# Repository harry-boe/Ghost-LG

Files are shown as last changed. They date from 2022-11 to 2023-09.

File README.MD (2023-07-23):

# Ghost LG Toolhead - RC2 18.07.23

## A V0 Toolhead using LGX Gears

| Ghost LG - Gearbox without front section to show Bondtech LG gears arangement | 
|--- |
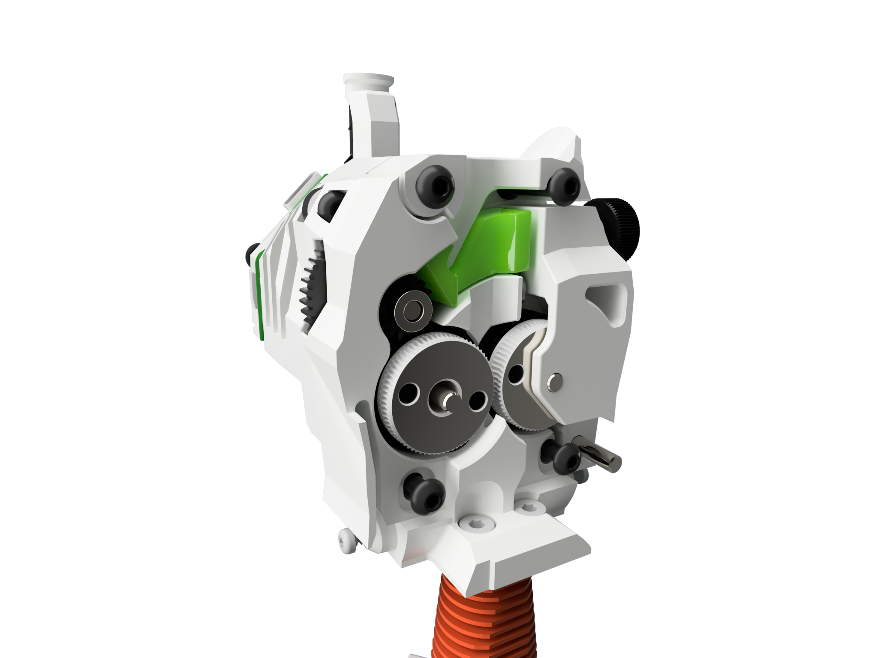
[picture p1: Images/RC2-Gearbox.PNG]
|  | 

This is the release candidate 2. This release is the result of extensive testing and pushing the toolhead to the limits.
Well i found the limits and started melting the plastic parts due to excessive stepper temps. And that's where this release kicks in.

Changes:
- Gearbox
  - Updated and strengthened idler
  - Updated beefier latch shuttle
  - Updated mid-section adopted to the new latch shuttle
- Motor Cover
  - Updated EBB35 mount with improved cooling and ventilation cut-outs
  - Updated pancake PCB mount 
- Cowling
	- Multiple minor changes to eliminate thin walls
	- Fix: Pinda probe mount. I did not had a Pinda probe to test so the old version mount was 1mm to small (diameter)

## Variations

### Hotends 

- Dragon style mounts 
    There are several hotends available that use the Drogon type mounting pattern including the Dragon itself, the dragon fly, Lizard, Lizard pro and others. In fact most of my testing was done with a red lizard
- Revo
  Currently one of the mor popular changes. The cowling as 2mm longer to adapt for the longer hotend. This version should provide improoved cooling as the smaller heat block allows for more airflow.

### Bed probes

- Euklid probe
  Most of my testing was done wit this probe. It looks kind of wierd but it works verry well.
  I'm using this probe with my Servo-Klicky dock.
- Zero Klick
  Another popular choice in the Ant printer universe.
  Should work as well with Servo Klicky dock and the standard Zero Klick docking solutions.
- Pinda Probe (SuperPinda)
  Inductive Probe if you don't like to deal with probe docking solutions

# Some impressions

| Ghost LG Toolhead | |
|--- |--- |
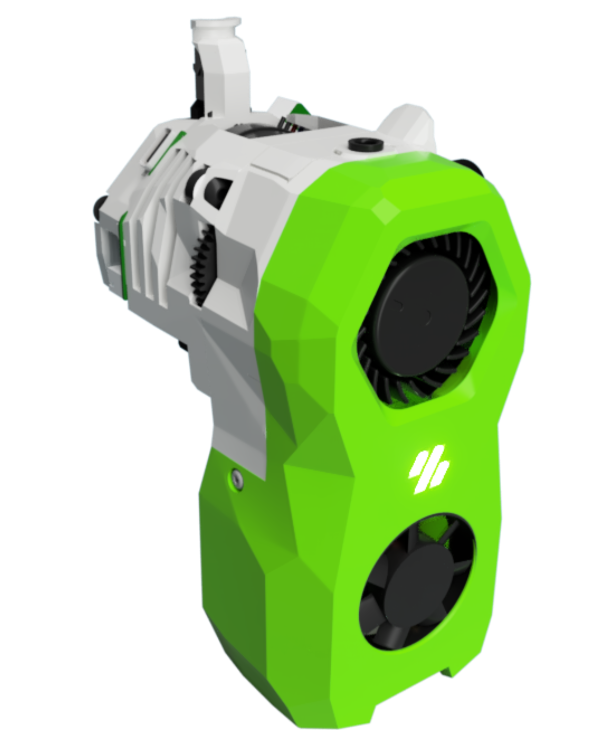
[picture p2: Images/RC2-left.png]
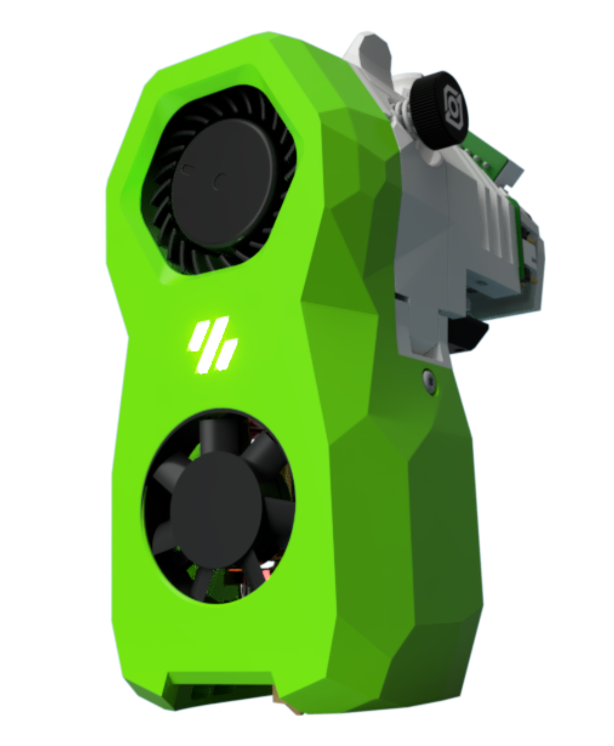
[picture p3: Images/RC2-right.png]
|  |  |

| Multiple Hotend and Probes | |
|--- |--- |
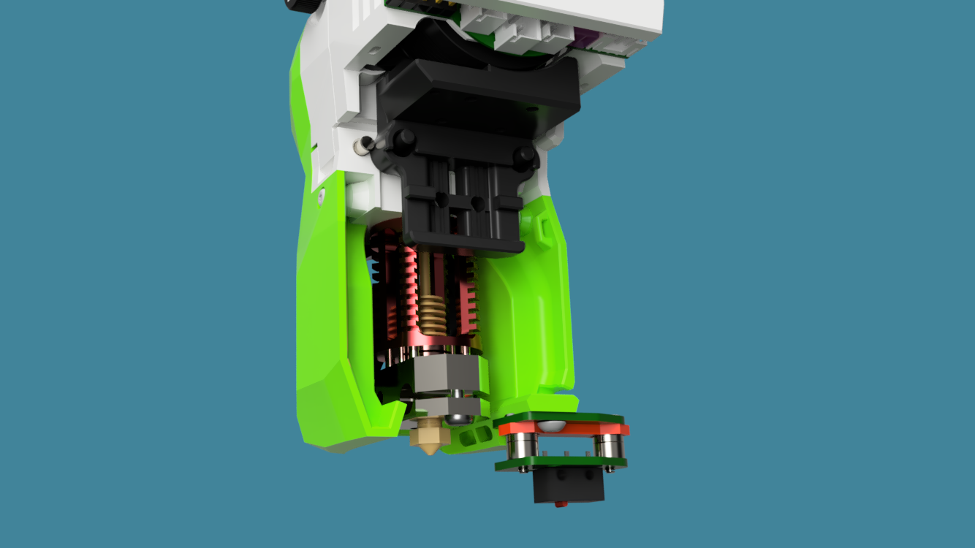
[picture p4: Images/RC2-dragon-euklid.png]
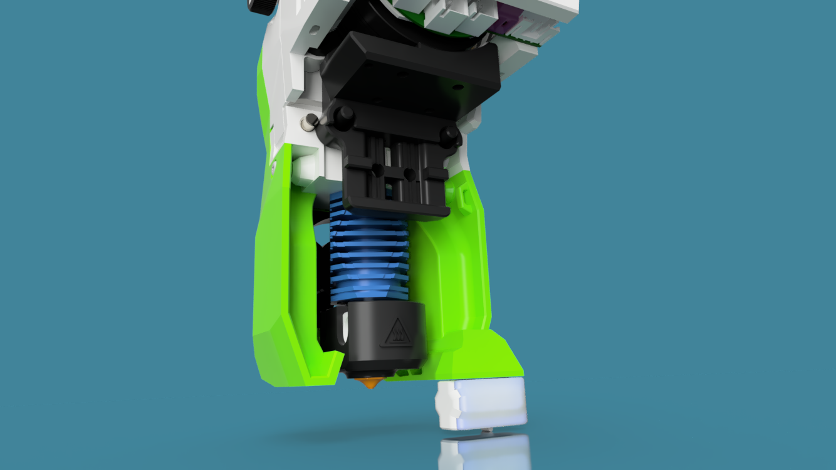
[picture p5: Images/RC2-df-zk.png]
|  |  |
| Dragon Hotend / Euklid Probe | Dragon-Fly / ZeroKlick Probe |
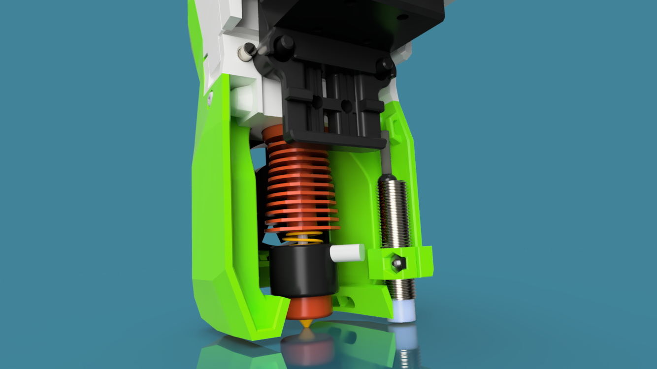
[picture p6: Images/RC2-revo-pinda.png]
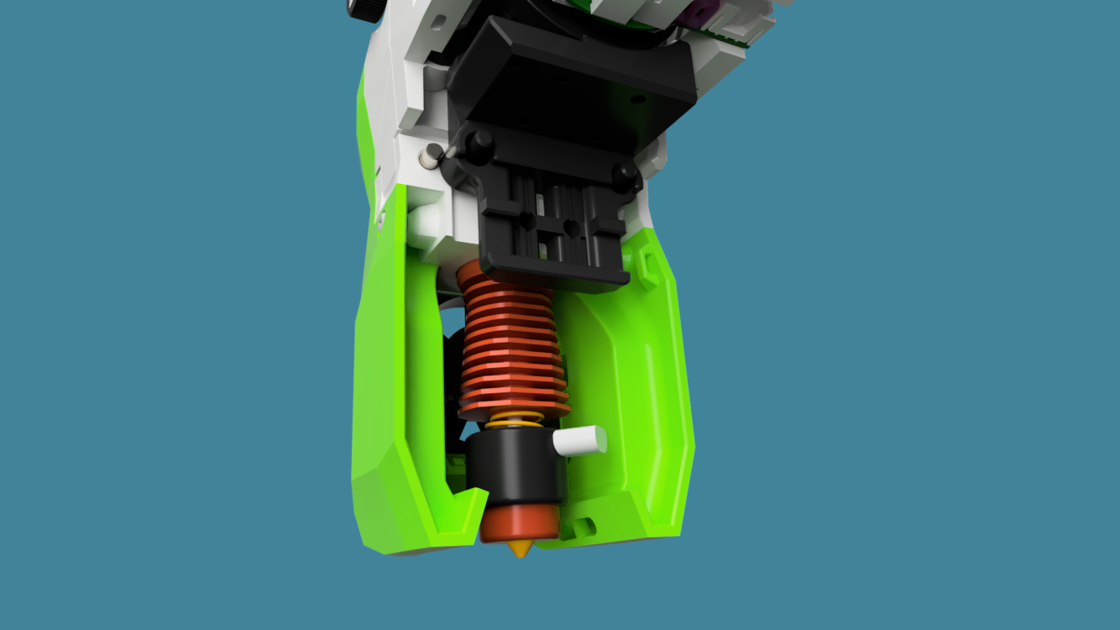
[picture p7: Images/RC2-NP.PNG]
|  |  |
| Revo / Pinda Probe | Revo / No Probe |

## Design Goals

-	Print Quality: 

    The Mini AB is hard to get right. Misalignment on the drive gears and also potential of centric gears due to the set screws affect print quality The LGX Gears solve this problem by running on needle bearings and not using set screws. They can also move axial on the bearings, which basically means that they are self-adjusting.
-	Maintain MINI AB footprint 

    At least on the important dimensions which are
	- Mount to front
    - Distance to Top (to maintain clearance with top-head)
    - Width (especially for IDEX use) 

The Ghost LG maintains those measurements by being 3mm smaller on width Distance to the back is +5mm (there is enough room here) Distance to the nozzle end is +4mm dragon and +6mm Revo. This means that the bed needs to be lowered by those distances. This is no Issue for the V0 and most of the Ant printers.

- Voron Design language Well basically the new stealth design

- Optimized for IDEX Minimize with (-3mm) Nozzle height adjustment. There is a slot for the mounting screws to the X-carriage to enable some height adjustment.

- Easy to assemble

## Printing notes

All parts print with standard Voron settings and no supports.
However the parts have fine details and tight tolerances. Make sure you printer is erll calibratd and use reasonable print speeds
Consider a brim for the EBB mount as the contact patch on the print bed is very small

## BOM

The project is stoill in its early stage so the BOM is subject to changes.
However I try to maintain the items below for the final design.

### Required Parts

| Item 	| Amount 	| Sourcing 	| Notes 	|
|---	|---	|---	|---	|
| HGX-Lite Etruder Gear Kit 	| 1 	| https://www.aliexpress.com/item/1005004699143725.html 	| Provided 3mm pins can be used but do not allign with case 	|
| 4015 Turbo Blower 40x40x15MM 	| 1 	| https://www.aliexpress.com/item/1005004909471864.html 	| Modifcation required  |
| 3007 axial fan 	| 1 	| 	|  |
| Hotend 	 | 1 	| Phaetos Dragon  	|  Revo in preparation |
| Nema 14 36mm pankake stepper motor	 | 1 	| 17mm or 20mm  	|  use the right rear cover  |
| M3x18 BHSC 	| 2 	| 	| 	|
| M3x20 BHSC 	| 2 	| 	| 	|
| M3x6 BHSC 	| 4 	| 	| 	|
| M3x6 countersunk flat head screws 	| 3 	| 	| 	|
| 2x8 or 2x10 self tapping screw 	| 2 	| 	| 	|
| M3 Heat Inserts | 6 	| 	| 	|
| PTFE Tube 	| 17mm | 	|  	 |

### Optional Parts

| Item 	| Amount 	| Sourcing 	| Notes 	|
|---	|---	|---	|---	|
| Individual NeoPixels 	 | 2 	| https://learn.adafruit.com/adafruit-neopixel-uberguide/individual-neopixels	| 	|
| 3x15mm Pin | 3 | https://www.aliexpress.com/item/1005002473550667.html | For those who want the pins alligned with the case |
| Omron Mouse Button - Micro Switch | 1 | | For filamentsensor (if üpossible) |
| 4.5 mmm Stainless Steel Solid Ball | 1 | https://www.aliexpress.com/item/1005004091669583.html | For filamentsensor (if üpossible) |

# Older Versions

# Ghost LG Toolhead - RC1 - 5.1.23

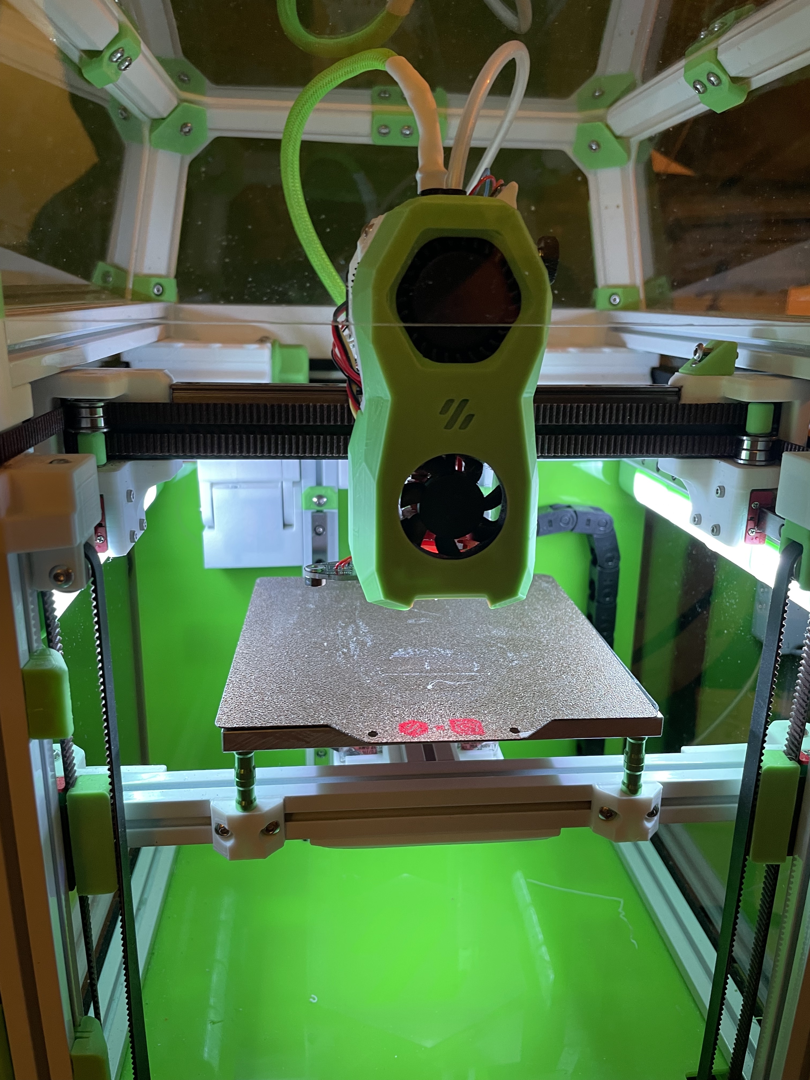
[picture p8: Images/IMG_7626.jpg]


New Features:

- Various cowling covers with mounts for probes
    - Euklic Probe - This is the one the I was using during the beta tests
      I'm using the euklid probe with my ServoKlicky dock
    - ZeroClick - mount for zruncho's clicky probe. The position as derived from the MiniAB, so it should work with the docks
    - PINDA inductive probe. Popular probe used on the Prusa MK3 printers. Maybe not the most accurate but defiantly the most hassle free installation.
      No Dock or complex macro definitions required. Not the klipper currently does not support the 4 wire probe with temp compensation in the firmware.
      If you like to have temp compensation make shure you order a Super PINDA (https://www.aliexpress.com/item/1005004488098625.html)
    - and last but not least a cover without any probe mounts

- New diffusor for Logo LED 
    - Maybe not for everybody as wiring is not easy.

- Anti squish adjustment thingy 
    - I don't think that's a requirement but a added one because this as popular right now

- Mounting screws for the cowling
    - The click on cowling came off a few times during my tests. So I added some self-tapping screws to mount it on the gearbox.
      This makes the whole toolhead way more rigid which is especially important for all cowling that have probes attached

Enhancements

- Cowling
    - fighting thin walls. Lots of tweaks here and there to improve printability 
    - New fan ducts. They are now moved forward like on the MiniSB. This allows for probe mounts without impact on the air channels
    - Improved air channels.
        The overall cooling performance is surprisingly good. But there was less cooling on the front side of the prints.
        The new air channels provide better flow in that area
    - Wiring channels
        The toolhead is now 2mm wider at the rear center (still same footprint). This creates more room for the wires exiting the toolhead
        Wire channel for cooling fan and nozzle LED redesigned.
        This section has now a break-away support which allows to route the wires without heaving to rempove the connectors.
        Also the cable channels are increased in size
    - Some minor design tweak on top of the toolhead for aesthetic reasons

- Gearbox
    - As mentioned the gearbox is now 2mm wider mid center (it not really visually noticeable)
    - Much wider cable channels to simplify wiring
    - New Latch geometry.
        The latch now pushed the idler back when opened (was a community suggestion)
    - Strengthened latch shuttle
    - Mid and rear section are bolted together with a countersunk screw.
        This make the toolhead much more rigid
    - Small changes on the idler to provide access to the anti-squish thing
    - the standard bowden collet is now the one from bondtech. It's much smaller and works better

- Board Mounts
    - EBB36 Mount
        - added a zip mount for the heater and thermistor wires
        - added a zip mount for the CANbus cable to eliminate stress on the connector and wires
    - The other mounts have no changes

## RC1 with EBB36 mount
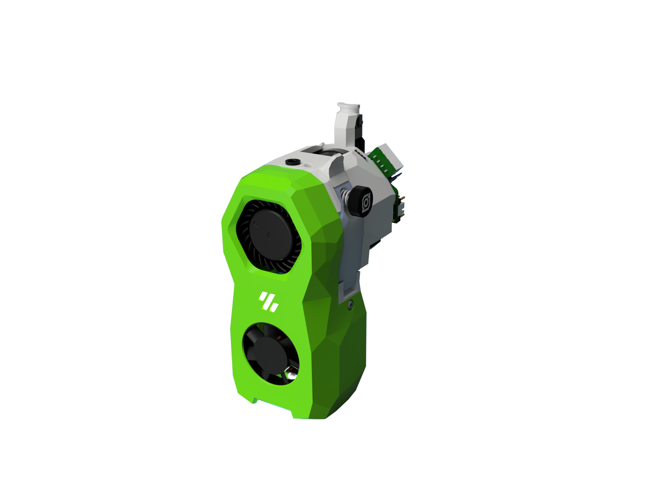
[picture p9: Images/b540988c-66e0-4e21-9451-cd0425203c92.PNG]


## PINDA Probe mount
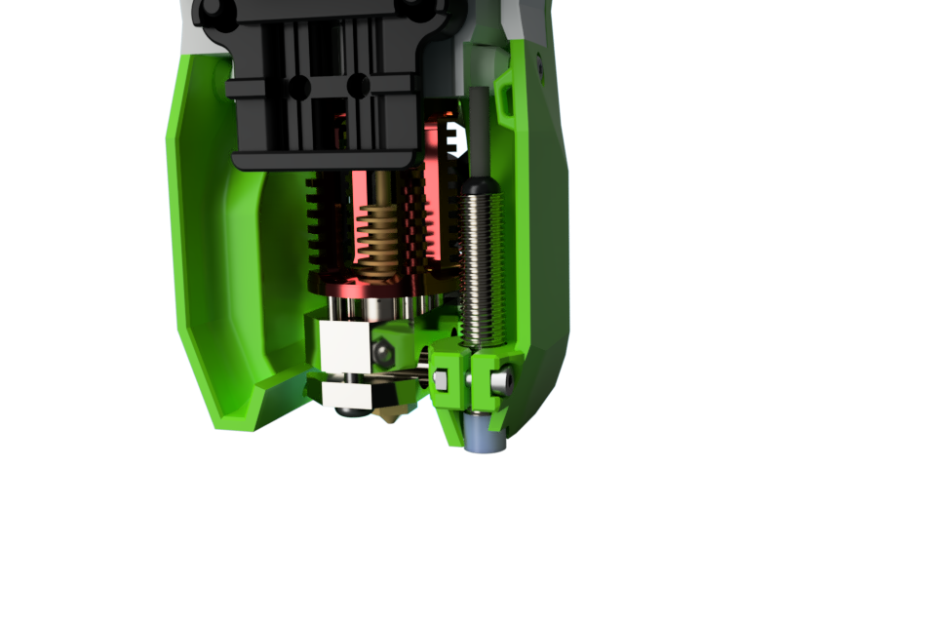
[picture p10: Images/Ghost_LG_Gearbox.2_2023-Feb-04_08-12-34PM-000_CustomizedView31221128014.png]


## Euklid Probe Mount
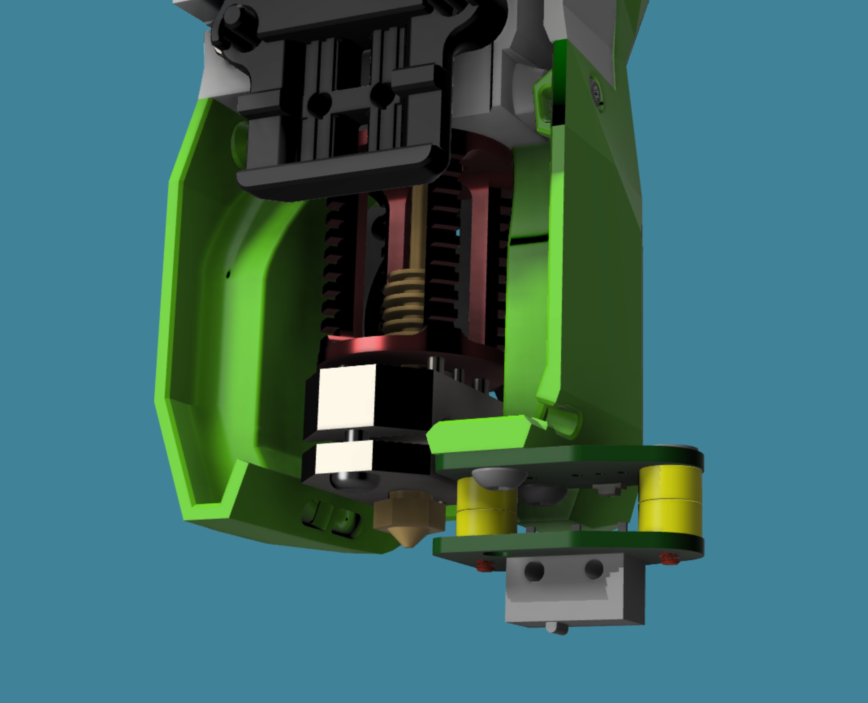
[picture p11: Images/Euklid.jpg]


## ZeroClick Probe Mount
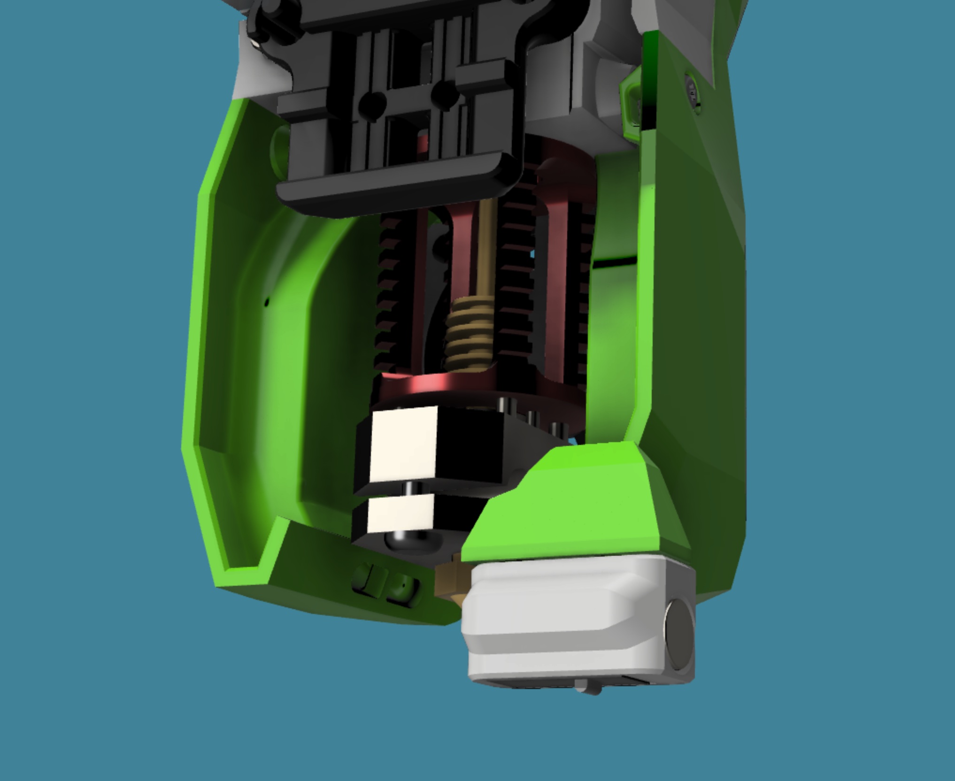
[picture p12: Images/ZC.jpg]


## Logo LED / Wire channel with break-away support / New fan ducts
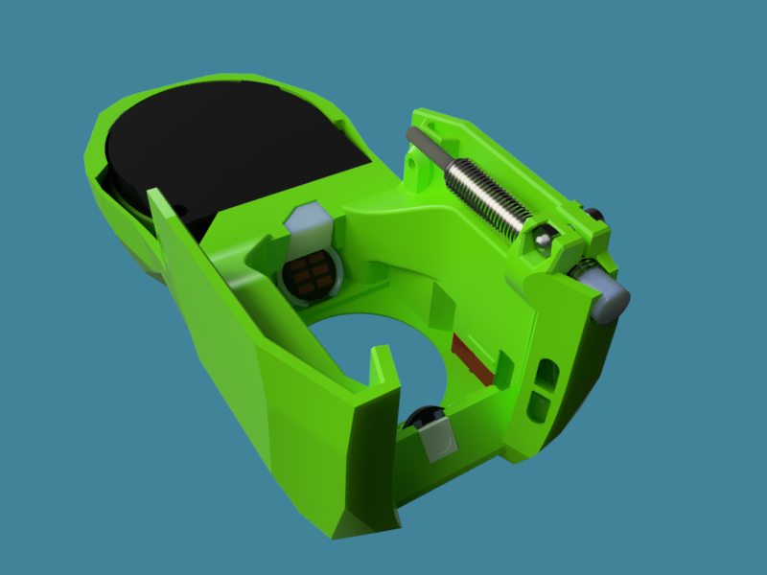
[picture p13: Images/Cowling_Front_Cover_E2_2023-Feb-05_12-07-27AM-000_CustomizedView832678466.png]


## New latch geometry / Anti-squish adjustment
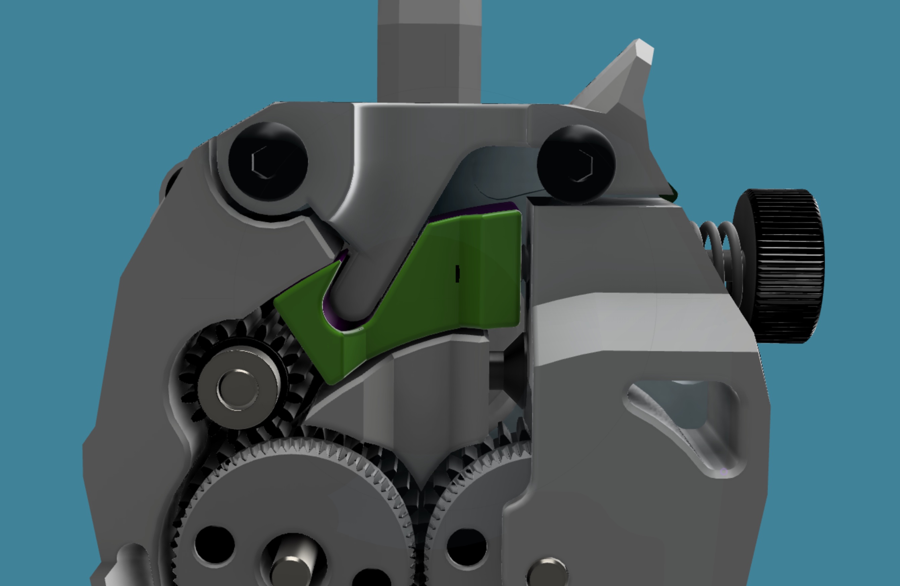
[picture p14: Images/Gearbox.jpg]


# [Changelog:](./CHANGELOG.MD)

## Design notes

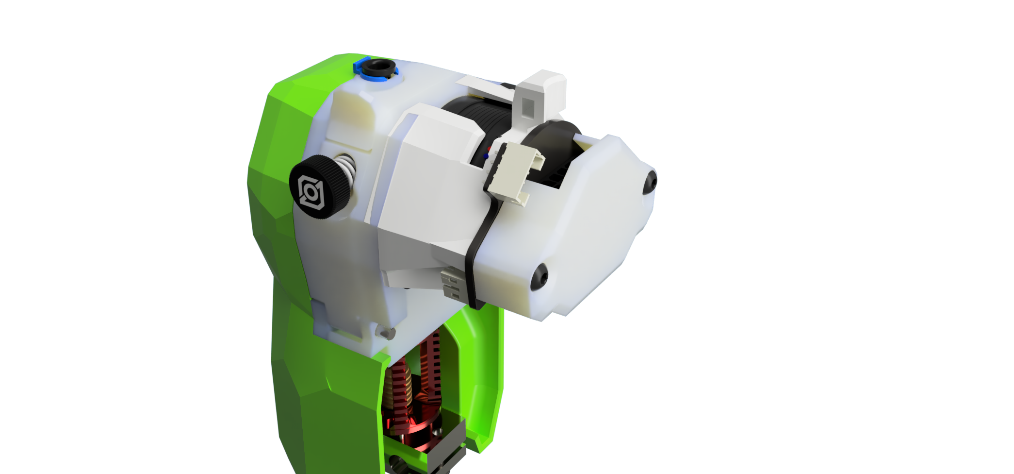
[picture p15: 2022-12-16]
Images/pc_02.PNG

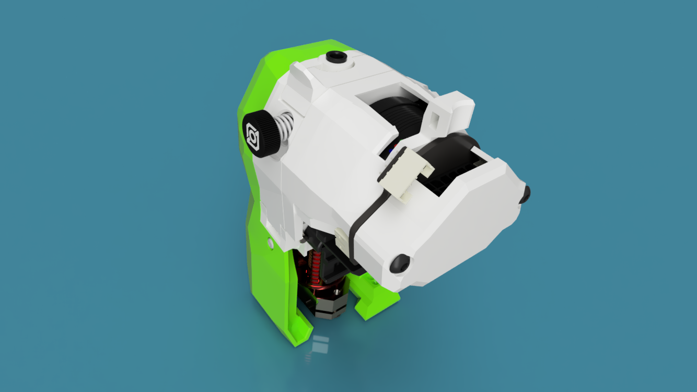
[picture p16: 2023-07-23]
Images/RC2-Pencake.png

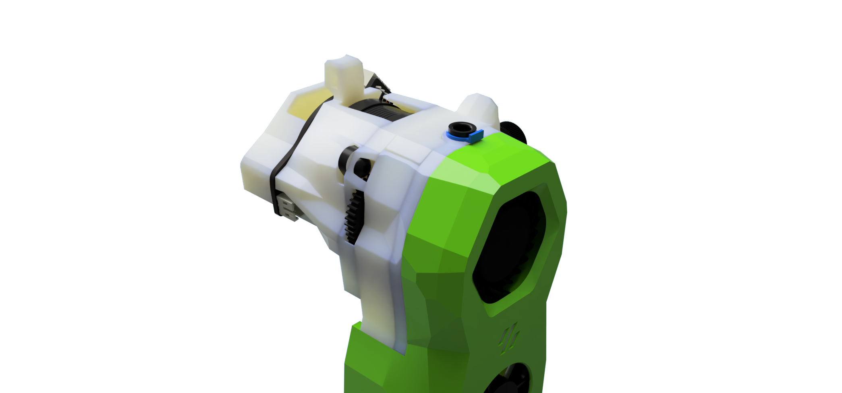
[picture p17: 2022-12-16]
Images/pc_01.PNG

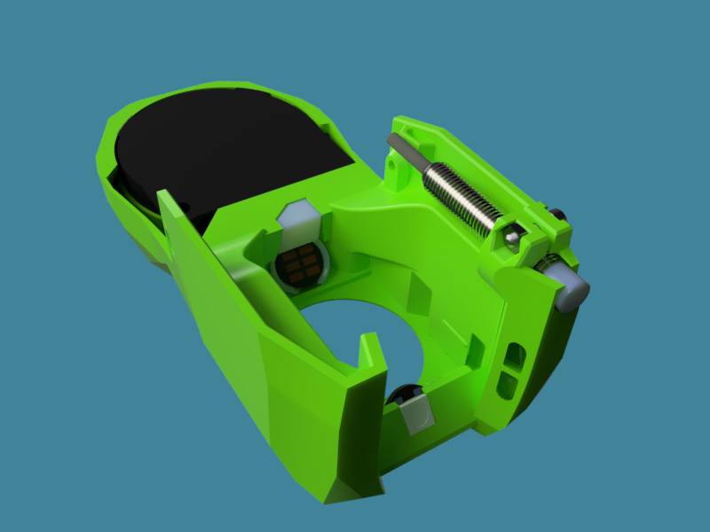
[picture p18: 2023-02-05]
Images/24e9c7e8-a816-45cc-8aab-17e264c7fdf0.PNG

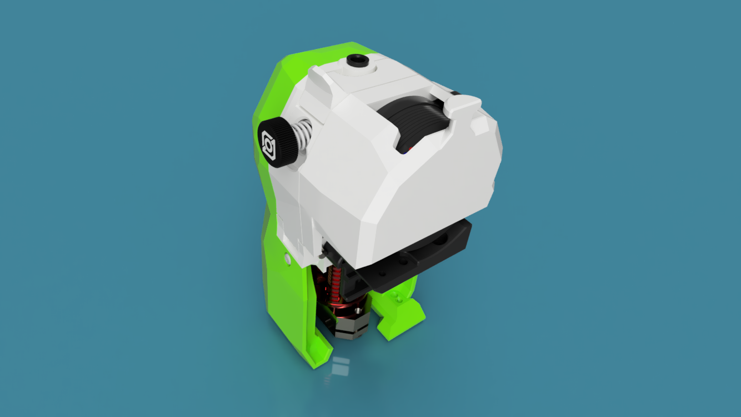
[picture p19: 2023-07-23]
Images/RC2-NoPCB.png

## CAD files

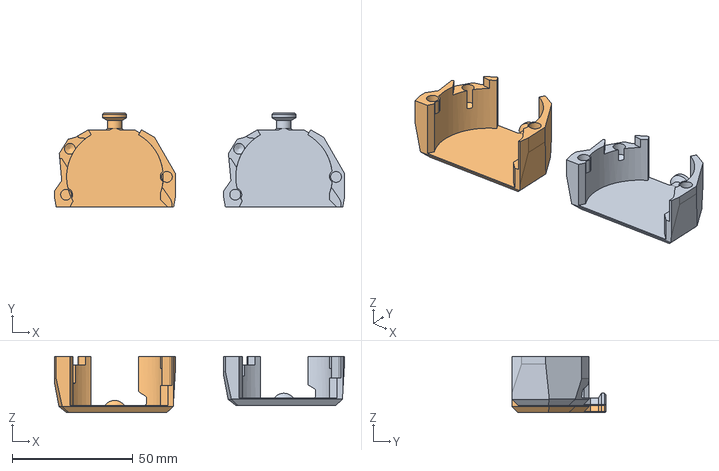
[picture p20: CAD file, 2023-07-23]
CAD/Cable Mount_RC2.step
120.0 x 39.0 x 23.2 mm
17mm
20 mm

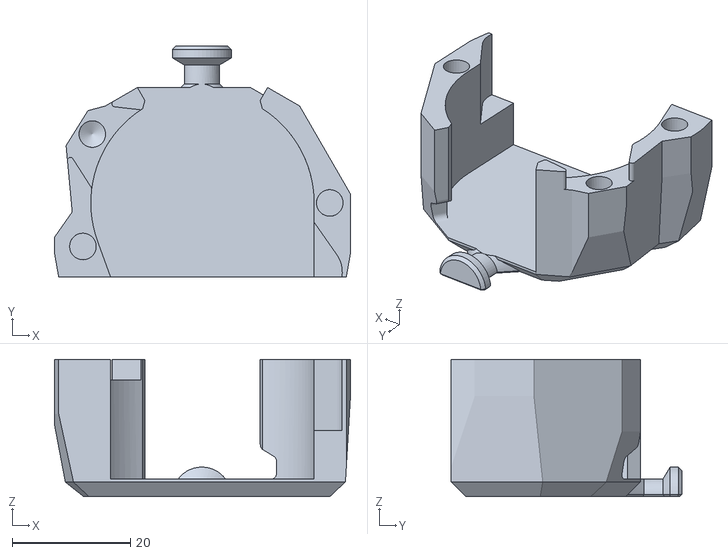
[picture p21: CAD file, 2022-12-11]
STLs/Cable_Mount/Cover_rear_20mm.stl
50.0 x 39.0 x 23.2

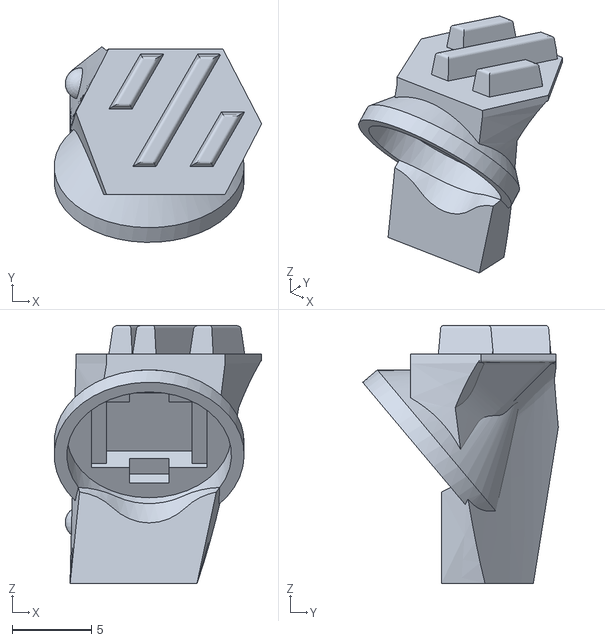
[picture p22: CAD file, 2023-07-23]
STLs/Cowling/[c]LED_Diffusor.stl
13.1 x 12.4 x 16.3

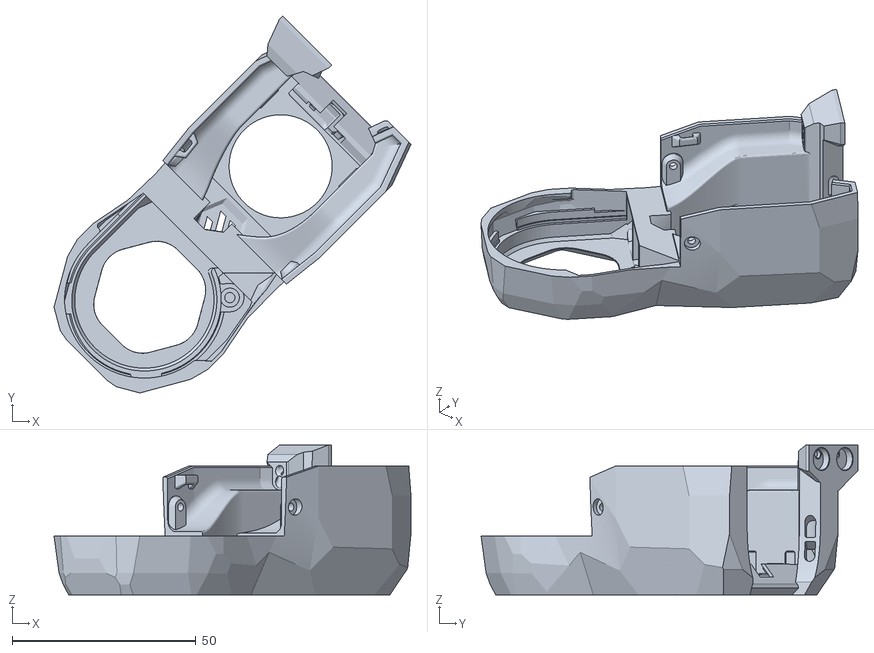
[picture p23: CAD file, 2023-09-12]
STLs/Cowling/Dragon/[a]Cowling_Dragon_ZeroKlick_RC2.stl
97.0 x 102.4 x 40.7

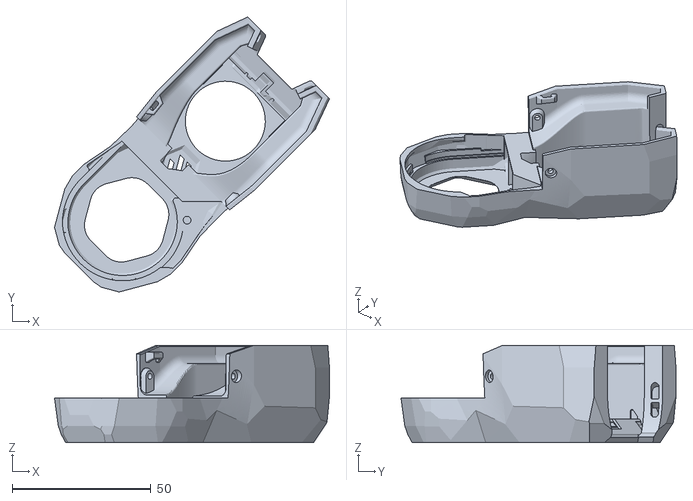
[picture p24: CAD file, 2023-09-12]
STLs/Cowling/Revo/[a]Cowling_Revo_RC2.stl
99.1 x 99.1 x 35.0

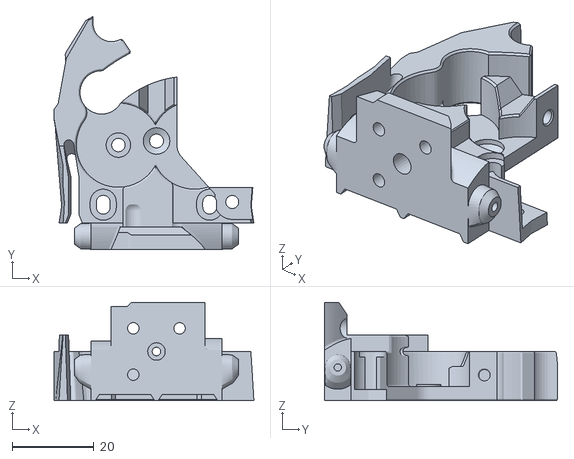
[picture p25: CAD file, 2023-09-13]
STLs/Gearbox/Dragon/Mid_Section_Dragon.stl
48.8 x 56.9 x 24.0

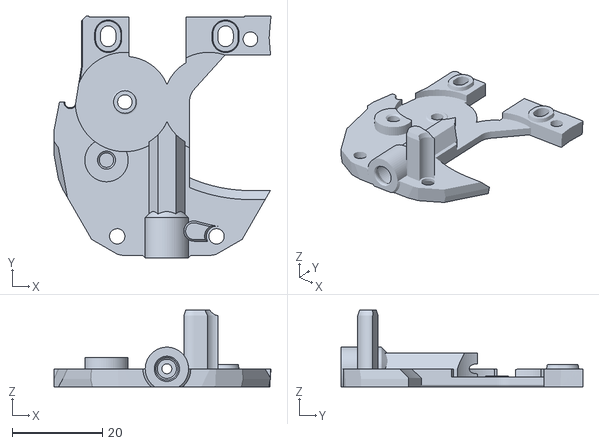
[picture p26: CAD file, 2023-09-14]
STLs/Gearbox/Front_Section_Pin_mod.stl
48.1 x 53.5 x 17.0

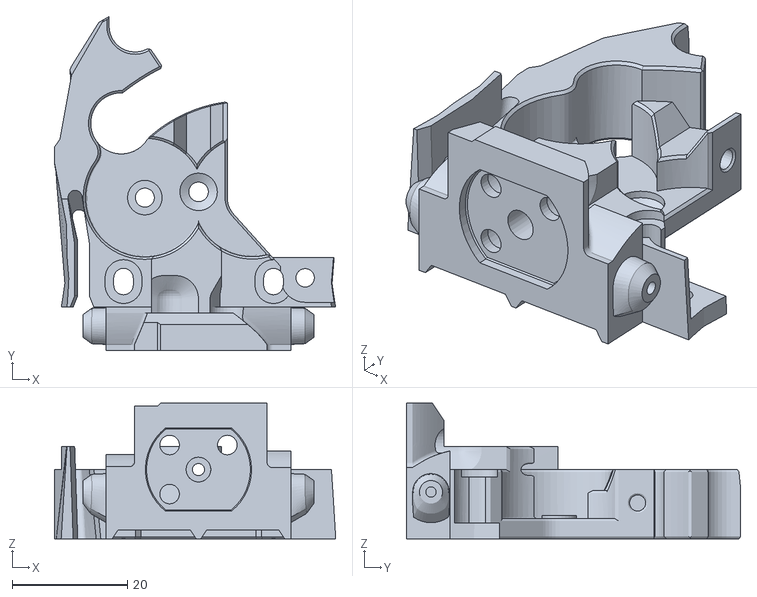
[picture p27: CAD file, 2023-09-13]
STLs/Gearbox/Revo/Mid_Section_Revo.stl
48.8 x 57.9 x 23.5

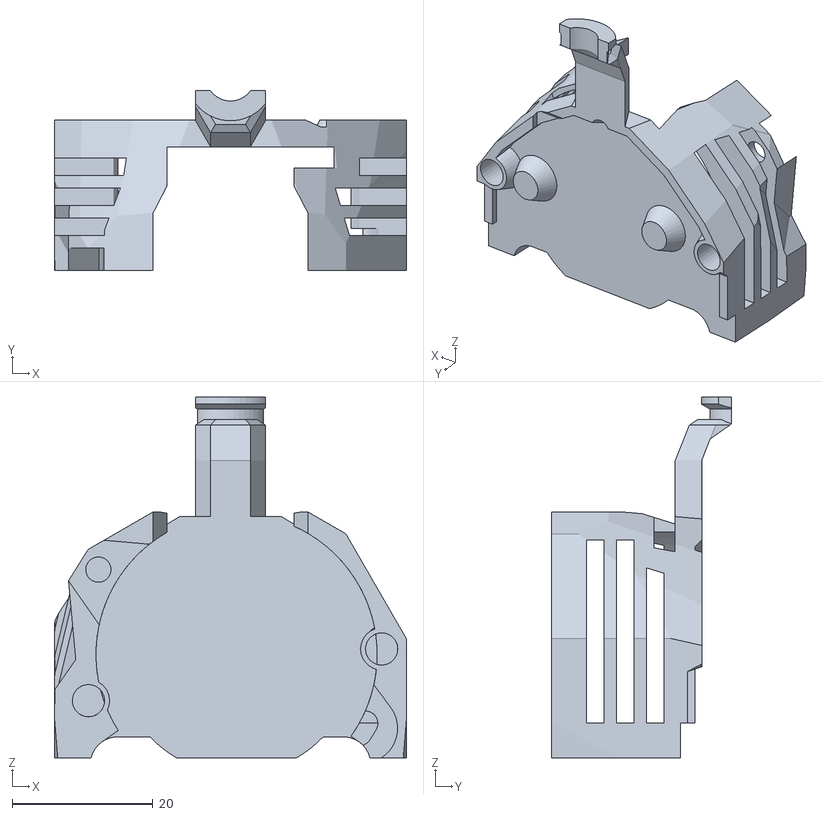
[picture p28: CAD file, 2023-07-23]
STLs/PCB_Mount_EBB36/PCB_Mount_EBB36_17mm.stl
50.1 x 25.6 x 51.3

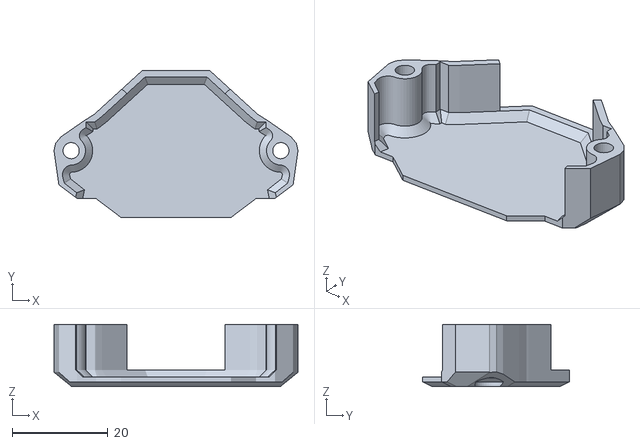
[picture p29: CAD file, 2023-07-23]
STLs/PCB_Mount_Pancake/Rear_Cover_Pancake v3.stl
51.1 x 30.8 x 13.0

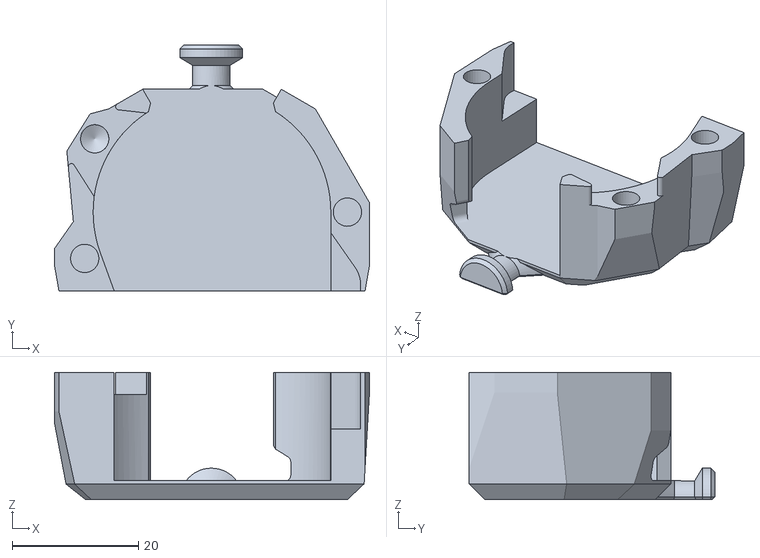
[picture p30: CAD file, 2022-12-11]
STLs/Cable_Mount/Cover_rear_17mm.stl
50.0 x 39.0 x 20.2

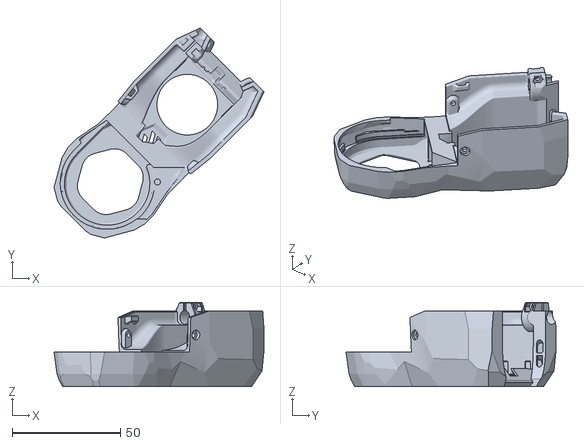
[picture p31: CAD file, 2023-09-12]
STLs/Cowling/Dragon/[a]Cowling_Dragon_Pinda_RC2.stl
97.0 x 97.0 x 39.0

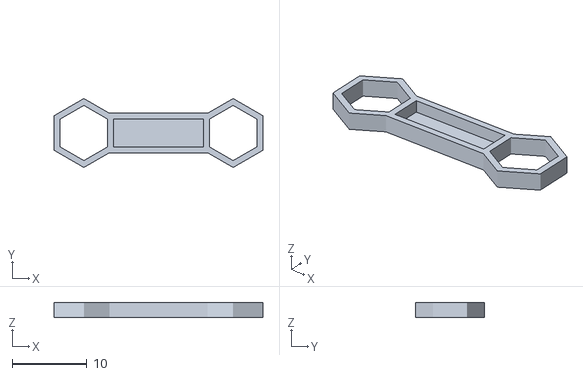
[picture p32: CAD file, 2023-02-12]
STLs/Cowling/Euklid_NoShort_Cover.stl
28.0 x 9.24 x 2.00

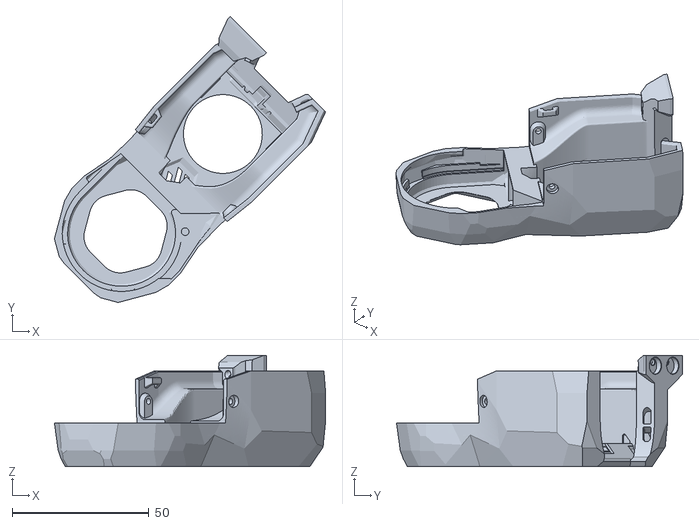
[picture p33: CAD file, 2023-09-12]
STLs/Cowling/Revo/[a]Cowling_Revo_ZeroKlick_RC2.stl
99.1 x 104.6 x 40.7

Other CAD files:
STLs/Gearbox/Rear Section.stl
STLs/PCB_Mount_EBB36/PCB_Cover_EBB36.stl
STLs/PCB_Mount_Pancake/PCB_Mount_Pancake_17mm.stl
STLs/Cowling/[c]diffusor.stl
STLs/Cowling/Dragon/[a]Cowling_Dragon_Euklid_RC2.stl
STLs/Cowling/Dragon/[a]Cowling_Dragon_RC2.stl
STLs/Cowling/Revo/[a]Cowling_Revo_Euklid_RC2.stl
STLs/Cowling/Revo/[a]Cowling_Revo_Pinda_RC2.stl
STLs/Gearbox/Front_Section.stl
STLs/Gearbox/Idler.stl
STLs/Gearbox/Latch.stl
STLs/Gearbox/Latch_schuttle.stl
STLs/Gearbox/Rear_Section.stl
STLs/Gearbox/Rear_Section_pin_mod.stl
STLs/PCB_Mount_EBB36/PCB_Mount_EBB36_20mm.stl
STLs/PCB_Mount_Pancake/PCB_Mount_Pancake_20mm.stl

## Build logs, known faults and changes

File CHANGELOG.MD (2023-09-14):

# Changelog

14.09.2023
- Re added Pin Mod
- Some repo restructuring

18.07.2023
- RC2 Release
  - Gearbox
    Updated and strengthened idler
    Updated beefier latch shuttle
    Updated mid-section adopted to the new latch shuttle
  - Motor Cover
    Updated EBB35 mount with improved cooling and ventilation cut-outs
    Updated pancake PCB mount
  - Cowling
    Multiple minor changes to eliminate thin walls
  - Fix: Pinda probe mount. I did not had a Pinda probe to test so the old version mount was 1mm to small (diameter)

21.03.2023
- 20mm EBB CAN Mount stl added

12.02.2023
- updated CAD file (assembled) - there where some parts missing in the CAD
- added a shortage prevention cover for the euklid probe
- bigger mounting holes for euklid probe to prevent braking the part

8.01.2023
- pin mod updated

5.01.2023 RC1
- see discription above
- note that the manual has not been updated yet
- same for the pin mod

06.01.2023
- new gearbox front STL for Bontech Push Collet
- updated mid section with locking bolts for cowling
- updated rear section with more room for cable management
- Cowling: bolt locking added. Updated cable channels
- New mount for BTT EBB 36 Can Bus boards 

15.12.2022
- Added a sub-folder in the STL's directory with part required for those using a stripped done LGX-Lite
- Added a sub-folder in the STL's directory with a mount and cover for the PanCake board
- Alternate gearbox front-section that uses a Bondtech Push-Fit collet instead on the E3D collet

12.12.2022:
- Draft Manual added

11.12.2022:  Beta-1
- Functional Extruder CAD and STL's released
- No bells and whistles for now. LED's and Filament sensor requires some more thonkering
- Basic Rear Cover added to help with cable managment
- Srepper gear mesh adjustmet added

05.12.2022:

- 1'st 1:1 prototype assembled
- went trough a compleate redesign for the cowling and the gearbox
- nothing to release yet, however the CAD is in the repo for a first review

## Some renderings of the new Design

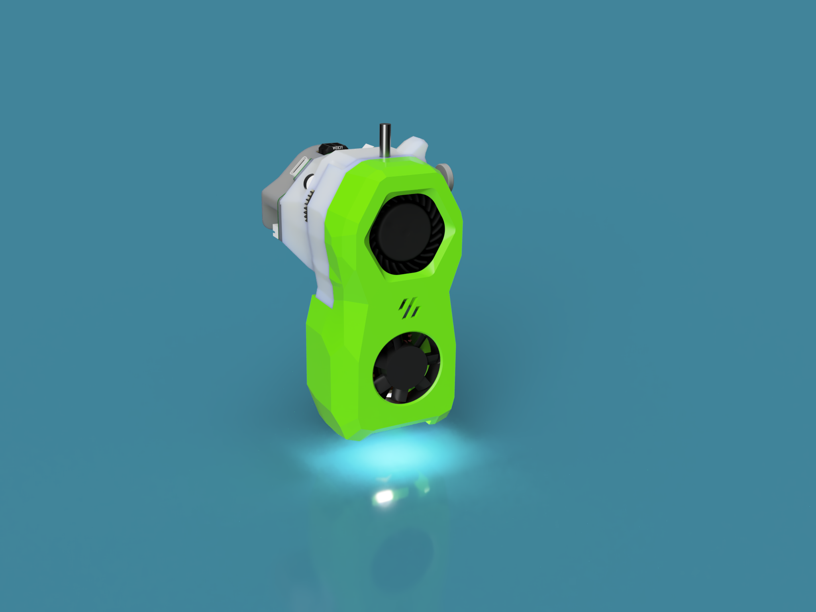
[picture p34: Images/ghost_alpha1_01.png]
Ghost 03

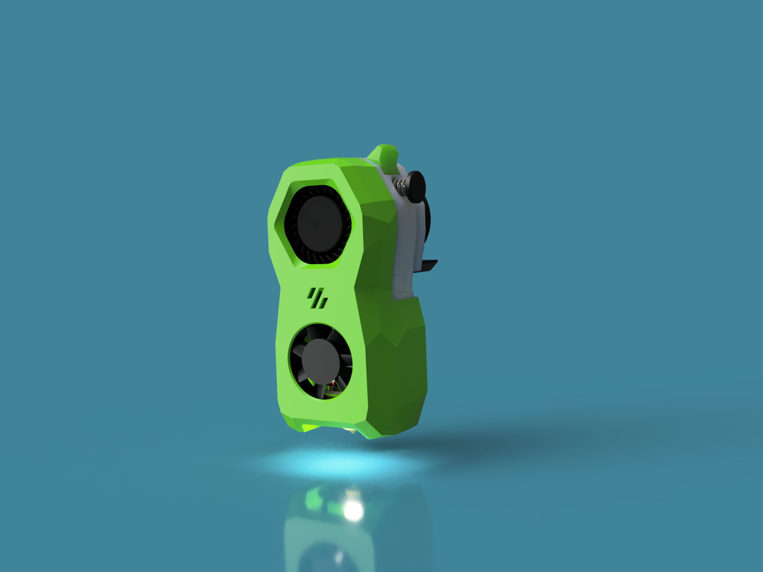
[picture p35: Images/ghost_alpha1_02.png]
Ghost 03

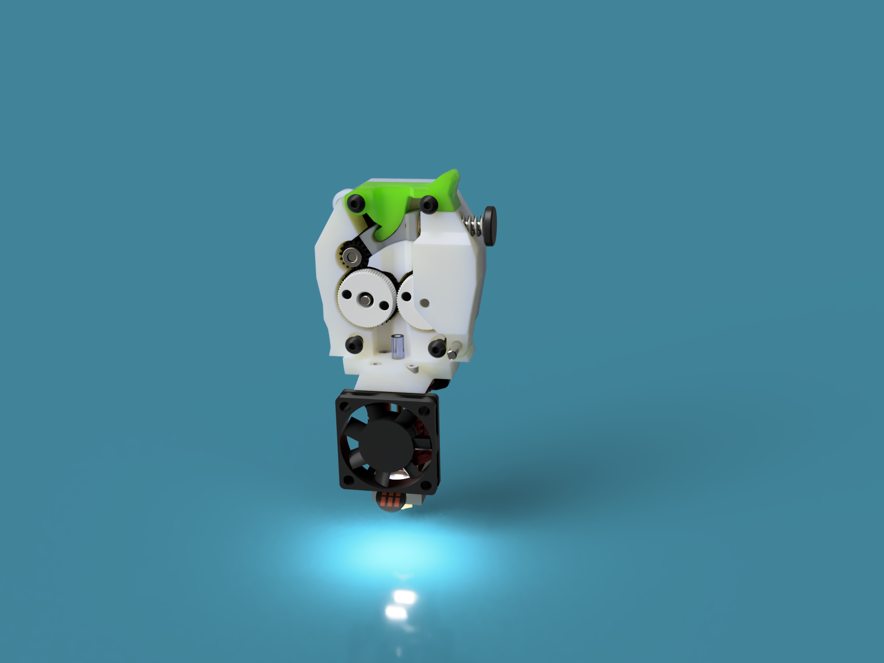
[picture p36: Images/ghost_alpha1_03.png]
Ghost 03


# Some first shots ..

https://user-images.githubusercontent.com/1899323/203817806-552646dd-b743-40ac-975e-db16fed9496d.mp4

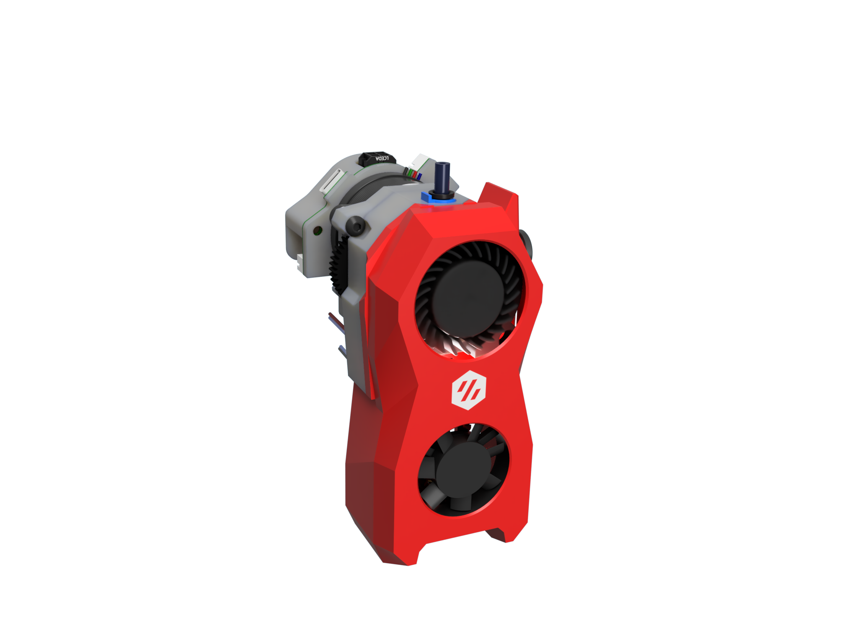
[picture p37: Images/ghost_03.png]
Ghost 03

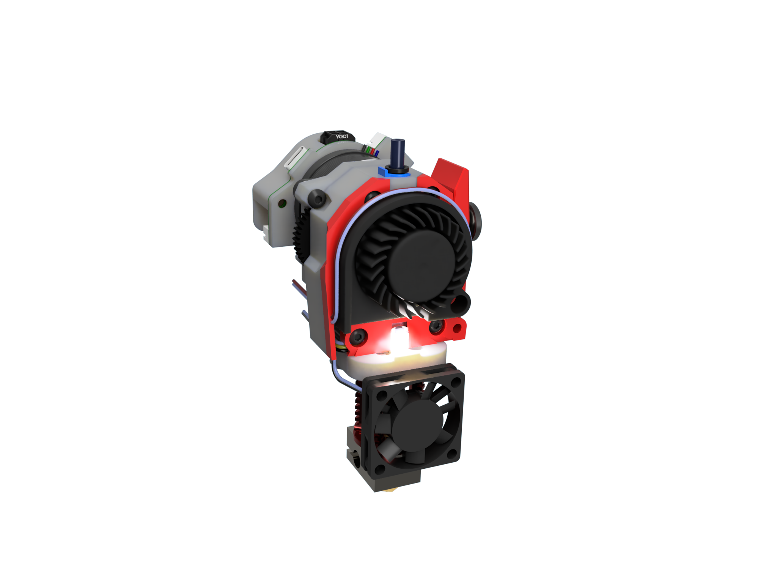
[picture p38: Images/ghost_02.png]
Ghost 02

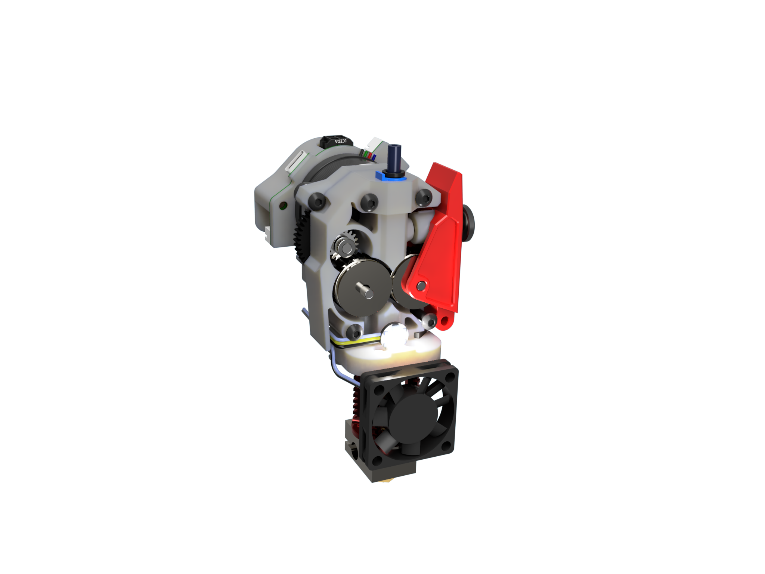
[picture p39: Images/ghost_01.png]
Ghost 01


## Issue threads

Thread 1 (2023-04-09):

Possibility to install on a v0.2 style X carriage?

gargamel778, 2023-04-09:
I printed the files and assembled the toolhead, I think it looks fantastic. Attached is the built piece.
...I then discovered that I can't use it on my v0.1, because I switched to a mini-SB a short while ago, which uses a different toolhead carriage.
Any chance the design can be adapted to suit?

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

harry-boe, 2023-04-13:
looks great

the V0.2 mount is fundamentally different than the v0.1 mount.
the steppers motor is raiser by +- 5mm due to the 3rd mount screw from the back

same for the ghost LG:  the stepper motor needs to raised as well to fit the mount and this will result I a entirely new geometry on the gearbox.

A V0.2 style ghost LG is on the bucket list but will not be ready soon.

Closed 2023-04-13.

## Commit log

2022-12-04 V2 - base for the real prototype
2022-12-07 BOM added
2022-12-11 Beta-1 released
    [Cover_rear_17mm.stl, Cover_rear_20mm.stl, Gearbox_front.stl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]
2022-12-11 updated rear cover stl
    [Gearbox_rear.stl]
2022-12-13 added stl for pin-mod
    [Gearbox_front_pin_mod.stl, Gearbox_rear_pin_mod.stl]
2022-12-13 stl print orientation fixed
    [Gearbox_front_pin_mod.stl]
2022-12-13 increased gear mesh spur gear
    [Gearbox_rear.stl, Gearbox_rear_pin_mod.stl]
2022-12-13 bondtech collet mod
    [Gearbox_front_pin_mod_btcollet.stl]
2022-12-13 BT Collet mod added
    [Gearbox_Front_Pin_btcollet_mod.stl, Gearbox_front_pin_mod_btcollet.stl]
2022-12-16 +pin-mod + PanCake mount
    [Gearbox_front_pin_mod.stl, Gearbox_mid_section_pin_mod.stl, Gearbox_rear_pin_mod.stl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]
2023-01-06 + EBBcan, gearbox updates, Cowling updates
    [EBBcan_PCB_Cover.stl, EBBcan_mount_17mm.stl, Gearbox_front_BT_Collet.stl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]
2023-01-06 cowling stl replaced with step file
2023-01-08 step file assembled ghost uploaded
2023-01-14 Bon Fan 3010 -> 3007
2023-02-05 RC1 Release
    [Cover_rear_17mm.stl, Cover_rear_20mm.stl, EBBcan_mount_17mm.stl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]
2023-02-05 Fixed Print orientation
    [EBBcan_mount_17mm.stl, Gearbox_front.stl, Idler.stl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]
2023-02-08 pin mod update
    [EBBcan_mount_17mm.stl, Gearbox_front.stl, Gearbox_front_pin_mod.stl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]
2023-02-12 updated CAD, added euklid cover
    [Euklid_NoShort_Cover.stl, [a]Cowling_Euklid.stl]
2023-03-21 20mm EBBcan Mount added
    [EBBcan_mount_20mm.stl]
2023-04-03 Ghost LG-R
    [EBBcan_PCB_Cover.stl, Gearbox_mid_Dragon.stl, Gearbox_mid_Revo.stl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]
2023-07-23 RC2 Release
    [Cable Mount_RC2.step, EBBcan_PCB_Cover.stl, EBBcan_mount_17mm.stl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]
2023-09-12 Optimized print orientation
    [[a]Cowling_Dragon_Euklid_RC2.stl, [a]Cowling_Dragon_Pinda_RC2.stl, [a]Cowling_Dragon_RC2.stl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]
2023-09-13 print orientation fixed
    [Mid_Section.stl]
2023-09-14 re added pin mod stl's
    [Front_Section_Pin_mod.stl, Rear Section.stl, Rear_Section_pin_mod.stl]
2023-09-14 print orientation
    [Front_Section.stl, Front_Section_Pin_mod.stl]
2023-09-14 stl's renamed
    [Mid_Section_Dragon.stl, Mid_Section_Revo.stl, Rear_Section.stl]
